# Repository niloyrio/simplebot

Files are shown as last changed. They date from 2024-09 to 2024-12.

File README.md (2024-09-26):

# SimpleBot

Bespoke Robot Society's original design for kids, students, or cost-sensitive tinkerers.

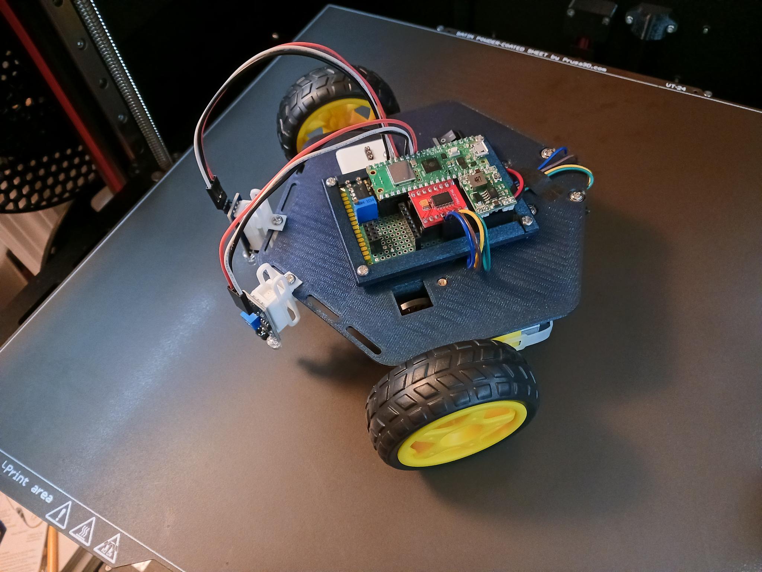
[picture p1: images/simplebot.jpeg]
Image of SimpleBot


Goals:

* Control a basic, multipurpose teaching robot with the Pi Pico (or Pico W).
* Demonstrate **optical odometry** - measuring the distance wheels turn by counting pulses on light sensors.
* Demonstrate **line following** - steer the robot in response to reflectance sensors that give the position of the line.
* Leave pins open on the microcontroller for additional upgrades.
* **Do not exceed $20 in price, with batteries included.**

## Hardware

Simplebot is based on the "Arduino Smart Car" kit that can be found on Amazon or Aliexpress. This provides a caster wheel, two yellow "TT" motors with optical encoder wheels and actual wheels, a power switch, and a 4xAA battery case. (~$6)

For line detectors, a generic "Infrared Obstacle Avoidance Sensor" module can be found in the US for 20 for $10 - SimpleBot requires two ($1).

Microcontroller - Raspberry Pi Pico ($4) or Raspberry Pi Pico W ($6).

Motor Controller - The TB6612FNG dual H-bridge module. You might be able to find this for $1 or less from overseas, but 3 for $9 is available in the US. ($3)

The optical encoder module requires one LED, one photoresistor, five resistors, and one LM393 chip for both. I don't know the prices for these, as I had them on hand.

an MPU6050 (Accelerometer/gyroscope) and nRF24l01 (2.4GHz radio module) are included on the circuit board, but haven't been tested or programmed yet. These occupy the I2C and SPI buses respectively, and would play well with some additional sensors (at the cost of spare pins for more SPI devices).

## Circuit Board

The protoboard design included uses all through-hole components.

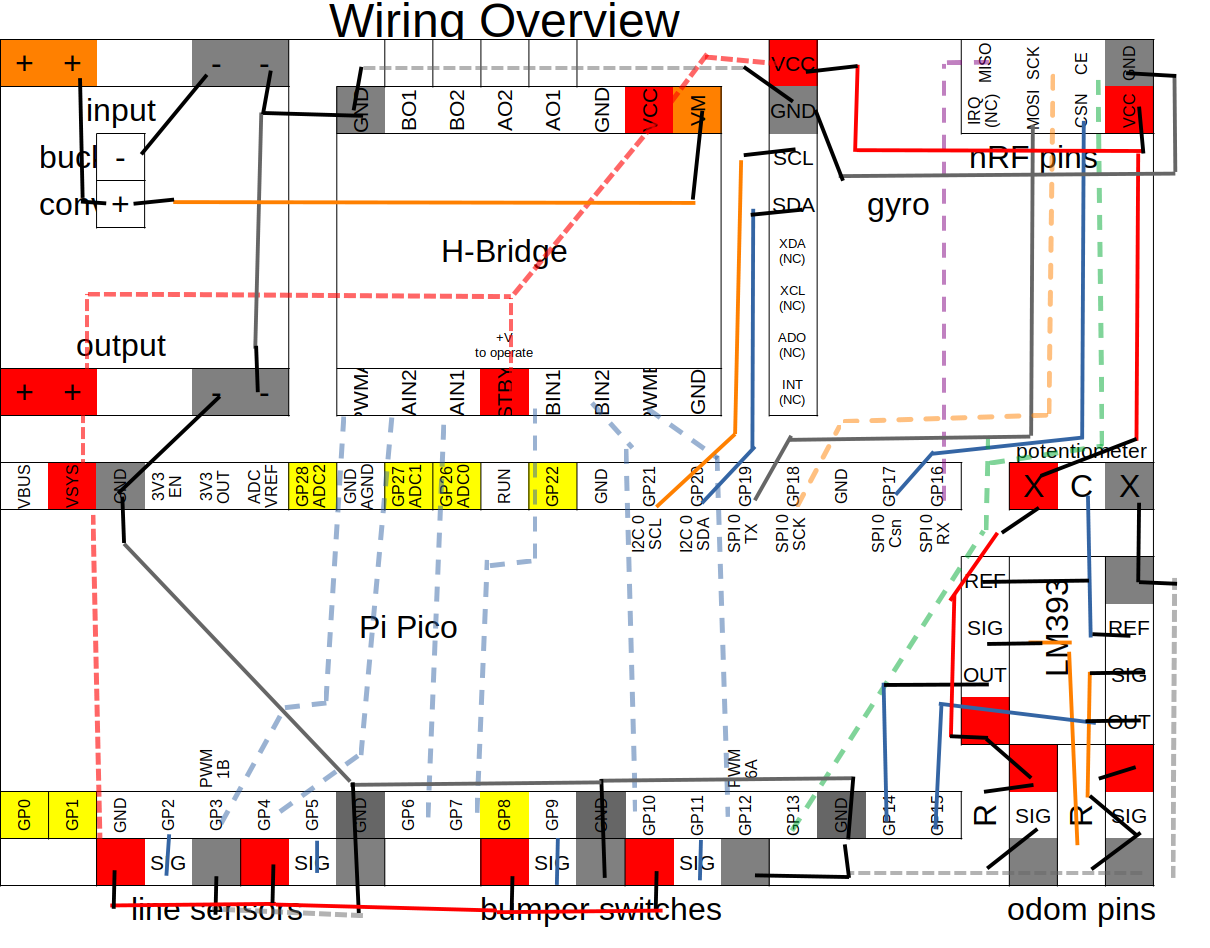
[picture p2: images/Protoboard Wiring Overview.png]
Wiring Diagram image


PCB design is still to-do.

The current protoboard pinout leaves 7 GPIOs open on the Pi Pico, including UART 0 and all three ADCs. 

## Software

Copy the included files to your Pi Pico by USB cable. I used Thonny to test the robot's programs.

# Future Work

Should I switch to an off-the-shelf optical encoder module, or should I build a custom line detecting sensor?

Printed circuit boards:

* Through hole soldering kit
* a board-on-board PCB - same layout as the protoboard, but soldered flat together.
* a custom PCB that uses the ICs from the modules directly

SimpleBot is unfortunately too large for standard micromouse mazes, so a "simplebot mini" seems to be in order.

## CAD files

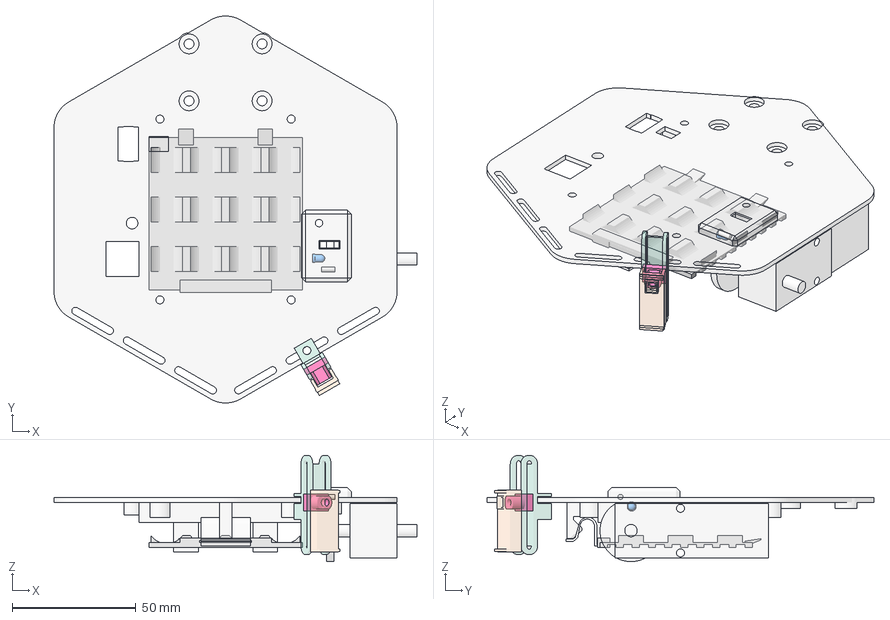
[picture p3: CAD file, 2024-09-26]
simplebot_CAD.FCStd
146.6 x 156.2 x 42.8 mm
baseplate
battery_case
OptoLED_mockup
opto_tht_R_mockup
optodometer
battery_hatch_v2
battery_hatch_clip_v2
line_sensor_sled_mount
line_sensor_sled
line_sensor_platform
motor_mockup

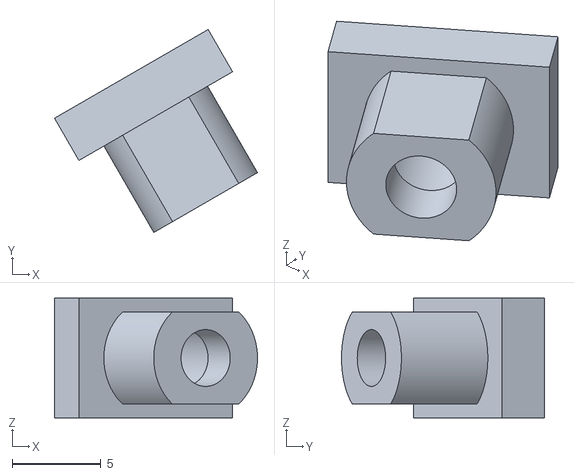
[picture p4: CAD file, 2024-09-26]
STL/line_sensor_sled.stl
11.4 x 11.4 x 6.75

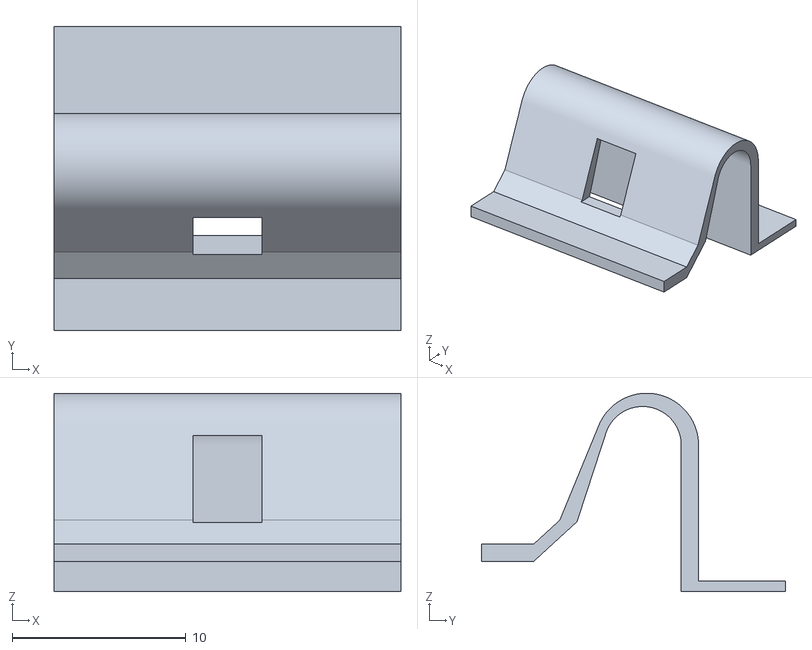
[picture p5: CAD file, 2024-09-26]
STL/battery_hatch_clip.stl
20.0 x 17.5 x 11.4

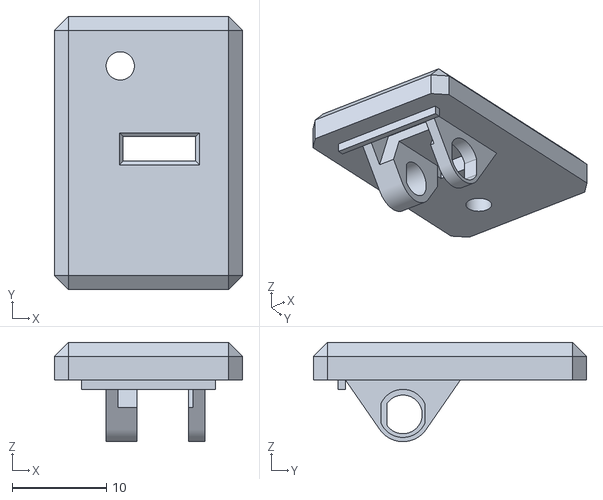
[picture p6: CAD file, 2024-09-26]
STL/optoencoder.stl
20.0 x 29.0 x 10.5

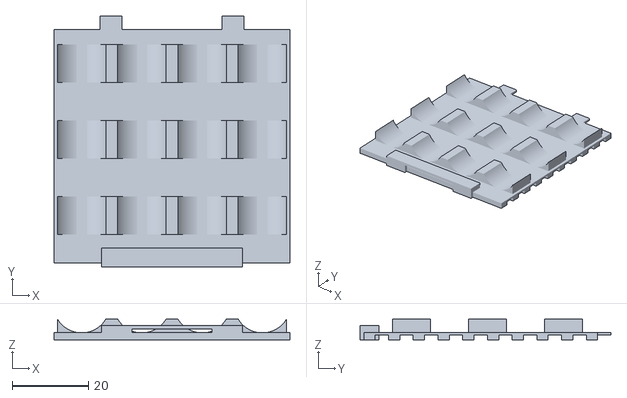
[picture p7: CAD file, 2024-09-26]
STL/battery_hatch.stl
62.0 x 66.0 x 5.50

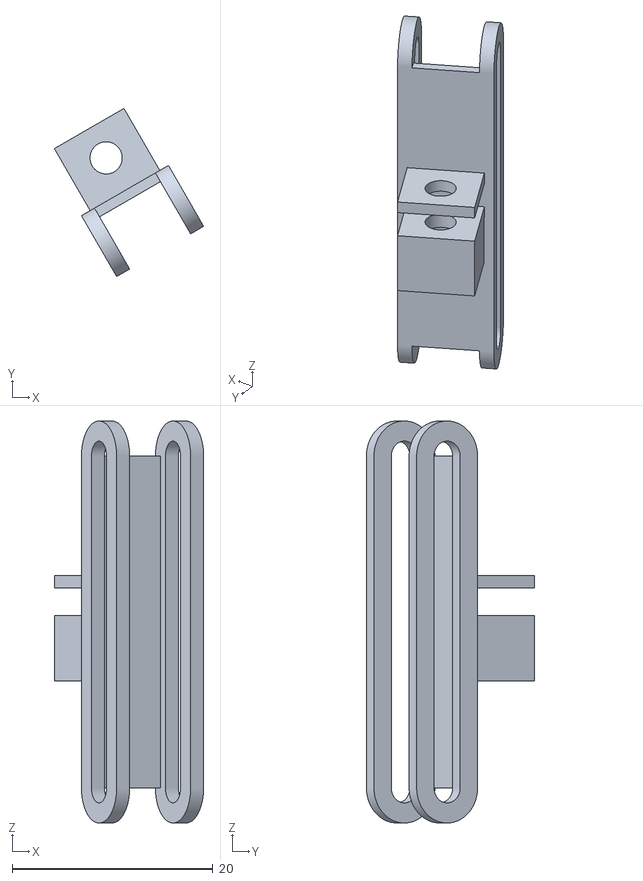
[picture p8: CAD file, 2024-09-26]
STL/line_sensor_sled_mount.stl
14.9 x 16.7 x 40.0

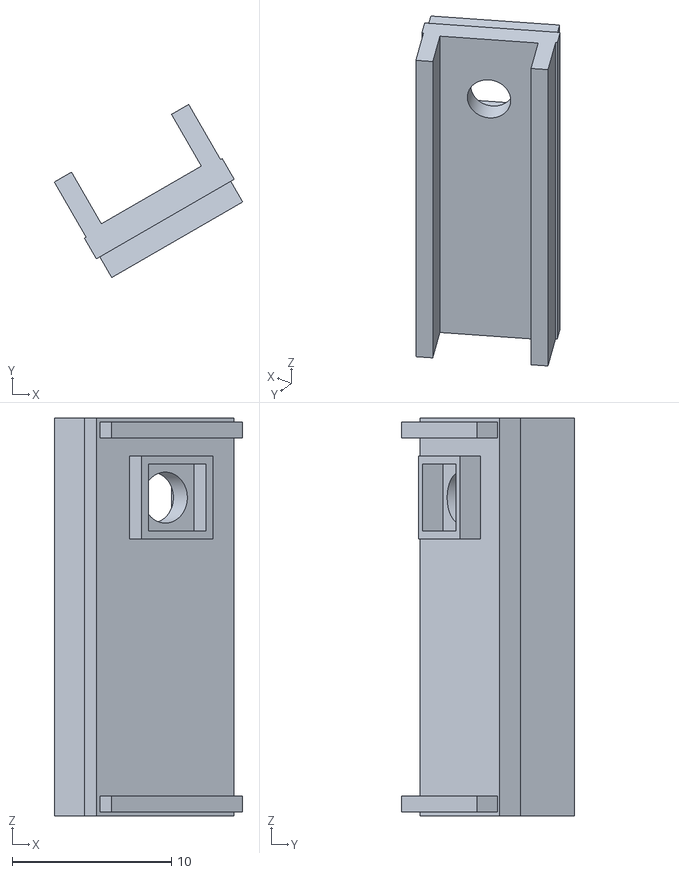
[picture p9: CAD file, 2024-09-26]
STL/line_sensor_sled_platform.stl
11.8 x 10.9 x 25.0

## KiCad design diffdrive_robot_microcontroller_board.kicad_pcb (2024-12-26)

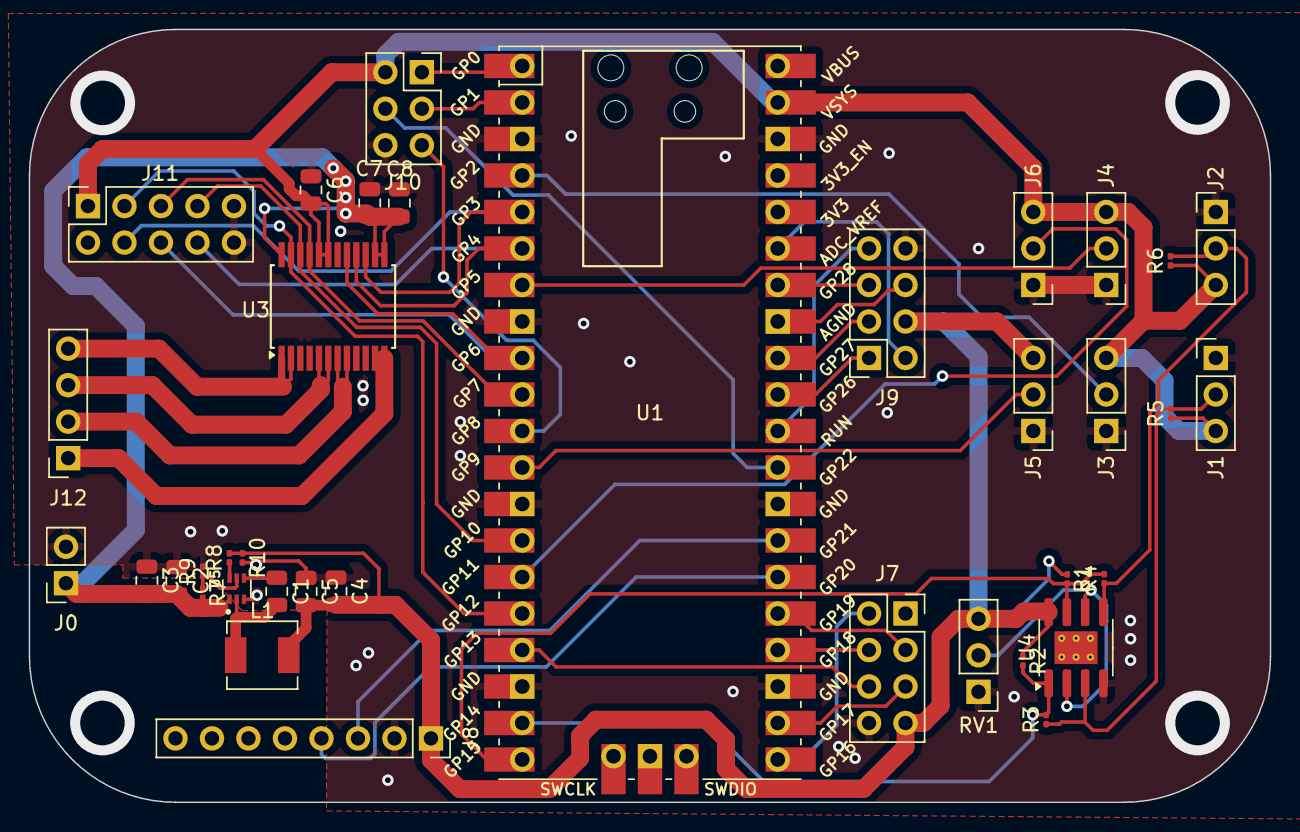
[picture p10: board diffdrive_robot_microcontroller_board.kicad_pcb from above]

Board: 2 copper layers, 86.4 x 53.8 mm, 37 parts (0 on the bottom side), 43 nets.

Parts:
C1, C2, C4, C6, C7: 100nF; C_0805_2012Metric
C3, C5, C8: 22uF; C_0805_2012Metric
J0: Battery_Input; PinSocket_1x02_P2.54mm_Vertical
J1: Odom L; PinHeader_1x03_P2.54mm_Vertical
J2: Odom R; PinHeader_1x03_P2.54mm_Vertical
J3: Sensor A; PinHeader_1x03_P2.54mm_Vertical
J4: Sensor B; PinHeader_1x03_P2.54mm_Vertical
J5: Sensor C; PinHeader_1x03_P2.54mm_Vertical
J6: Sensor D; PinHeader_1x03_P2.54mm_Vertical
J7: nRF24L01 Connector; PinSocket_2x04_P2.54mm_Vertical
J8: i2c accel/gyro; PinSocket_1x08_P2.54mm_Vertical
J9: analog_expansion; PinSocket_2x04_P2.54mm_Vertical
J10: digital_expansion; PinSocket_2x03_P2.54mm_Vertical
J11: external_hbridge; PinSocket_2x05_P2.54mm_Vertical
J12: Motor_Pins; PinSocket_1x04_P2.54mm_Vertical
L1: 2.2uH; L_Sunlord_MWSA0402S
R1, R2: 1k; R_0201_0603Metric
R3, R4: R_hysteresis; R_0201_0603Metric
R5, R6, R7: 100K; R_0201_0603Metric
R8: 30.9K; R_0201_0603Metric
R9: 15.4K; R_0201_0603Metric
R10: 10K; R_0201_0603Metric
RV1: R_Potentiometer; PinHeader_1x03_P2.54mm_Vertical
U1: Pico; RPi_Pico_SMD_TH
U3: TB6612FNG; SSOP-24_5.3x8.2mm_P0.65mm
U4: LM393; SOIC-8-1EP_3.9x4.9mm_P1.27mm_EP2.29x3mm_ThermalVias
U5: TPS562242DRLR; SOT50P160X60-6N

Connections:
+3V3: C4.2, C5.2, C6.2, J1.3, J2.3, J3.3, J4.3, J5.3, J6.3, J7.7, J8.1, J9.4, J10.2, J11.1, J11.2, L1.2, R1.1, R2.1, R5.1, R6.1, R8.2, R10.1, RV1.3, U1.39 (VSYS), U3.19 (STBY), U3.20 (VCC), U4.8 (V+)
+BATT: C2.2, C3.2, C7.2, C8.2, J0.1, R7.2, U3.13 (VM2), U3.14 (VM3), U3.24 (VM1), U5.1 (VIN)
ADC0: J9.1, U1.31 (GPIO26_ADC0)
ADC1: J9.3, U1.32 (GPIO27_ADC1)
ADC2: J9.5, U1.34 (GPIO28_ADC2)
AGND: J9.6, U1.33 (AGND)
AIN1: J11.5, U1.10 (GPIO7), U3.21 (AIN1)
AIN2: J11.7, U1.14 (GPIO10), U3.22 (AIN2)
AVREF: J9.2, U1.35 (ADC_VREF)
BIN1: J11.6, U1.9 (GPIO6), U3.17 (BIN1)
BIN2: J11.8, U1.6 (GPIO4), U3.16 (BIN2)
CE: J7.6, U1.17 (GPIO13)
CSN: J7.5, U1.22 (GPIO17)
GND: C2.1, C3.1, C4.1, C5.1, C6.1, C7.1, C8.1, J0.2, J1.1, J2.1, J3.1, J4.1, J5.1, J6.1, J7.8, J8.2, J9.8, J10.6, J11.9, J11.10, R9.2, R10.2, RV1.1, U1.3 (GND), U1.8 (GND), U1.13 (GND), U1.18 (GND), U1.23 (GND), U1.28 (GND), U1.38 (GND), U3.3 (PGND1), U3.4 (PGND1), U3.9 (PGND2), U3.10 (PGND2), U3.18 (GND), U4.4 (V-), U5.3 (GND)
GP0: J10.1, U1.1 (GPIO0)
GP1: J10.3, U1.2 (GPIO1)
GP8: J10.5, U1.11 (GPIO8)
GP22: J10.4, U1.29 (GPIO22)
MISO: J7.2, U1.21 (GPIO16)
MOSI: J7.3, U1.25 (GPIO19)
unnamed: J1.2, R3.1, R5.2, U4.3 (+)
unnamed: J2.2, R4.1, R6.2, U4.5 (+)
unnamed: J3.2, U1.4 (GPIO2)
unnamed: J4.2, U1.7 (GPIO5)
unnamed: J5.2, U1.12 (GPIO9)
unnamed: J6.2, U1.15 (GPIO11)
unnamed: J12.1, U3.11 (BO1), U3.12 (BO1)
unnamed: J12.2, U3.7 (BO2), U3.8 (BO2)
unnamed: J12.3, U3.5 (AO2), U3.6 (AO2)
unnamed: J12.4, U3.1 (AO1), U3.2 (AO1)
unnamed: R2.2, R3.2, U1.19 (GPIO14), U4.1
unnamed: R1.2, R4.2, U1.20 (GPIO15), U4.7
unnamed: RV1.2, U4.2 (-), U4.6 (-)
unnamed: C1.1, U5.4 (BST)
unnamed: R7.1, R9.1, U5.5 (EN)
unnamed: R8.1, U5.6 (FB)
PWMA: J11.3, U1.16 (GPIO12), U3.23 (PWMA)
PWMB: J11.4, U1.5 (GPIO3), U3.15 (PWMB)
RUN: J9.7, U1.30 (RUN)
SCK: J7.4, U1.24 (GPIO18)
SCL: J8.3, U1.27 (GPIO21)
SDA: J8.4, U1.26 (GPIO20)
SW: C1.2, L1.1, U5.2 (SW)

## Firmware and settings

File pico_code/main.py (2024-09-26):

from machine import Pin
import time
from motor import Motor
from bot import SimpleBot

# black tape = high (1), brighter surface = low (0)
l, r = Pin(9, Pin.PULL_DOWN), Pin(11, Pin.PULL_DOWN)

values = [0, 0]

m = Motor(3, 4, 6)
n = Motor(12, 7, 10)        
bot = SimpleBot(m, n)
while True:
    _l = l.value()
    _r = r.value()
    if _r and _l:
        bot.reverse(30)
    elif _l:
        bot.ccw(30)
    elif _r:
        bot.cw(30)
    else:
        bot.forward(30)
    time.sleep(0.05)

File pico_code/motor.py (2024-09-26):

from machine import Pin, PWM

class Motor:
    def __init__(self, pwm_pin, in1_pin, in2_pin):
        self.pwm = PWM(Pin(pwm_pin), freq=50, duty_u16=8192)
        self.pwm.duty_u16(0) # 0%
        self.dir_pins = (Pin(in1_pin, Pin.OUT), Pin(in2_pin, Pin.OUT))
        
    def forward(self, speed=None):
        self.dir_pins[0].value(0)
        self.dir_pins[1].value(1)
        if speed: self.speed(speed)
        
    def reverse(self, speed=None):
        self.dir_pins[1].value(0)
        self.dir_pins[0].value(1)
        if speed: self.speed(speed)
        
    def stop(self):
        self.dir_pins[0].value(0)
        self.dir_pins[1].value(0)
    
    def speed(self, percent):
        self.pwm.duty_u16(int((percent/100) * 65535)) # 0%

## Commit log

2024-09-26 initial release
    [battery_hatch.stl, battery_hatch_clip.stl, line_sensor_sled.stl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]
2024-09-26 Wiring Diagram
2024-09-26 Add wiring diagram to README
2024-12-26 Add files via upload
    SMD Version of the PCB
    [diffdrive_robot_microcontroller_board.kicad_pcb]
